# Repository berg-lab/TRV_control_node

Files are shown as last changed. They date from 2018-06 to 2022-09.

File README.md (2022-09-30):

# TRV_control_node
First generation radiator control based on Raspberry Pi Zero W

Refer to Paper: [Development and evaluation of an automatic steam radiator control system for retrofitting legacy heating systems in existing buildings](https://www.sciencedirect.com/science/article/abs/pii/S0378778821006289)

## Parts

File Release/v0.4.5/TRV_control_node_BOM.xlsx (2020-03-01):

Qty | Parts | Value | MPN | Device | Package | Description | PRICE
2 | RX, TX | LED | LG R971-KN-1 | LEDCHIPLED_0805 | CHIPLED_0805 | LED
1 | U4 | PCA9685 | PCA9685BS,118 | PCA9685HVQFN28 | HVQFN28_SOT788-1 | 16-channel 12-bit PWM
6 | C5, C6, C7, C11, C12, C15 | 0.1uF | GRM155R71C104KA88J | MICROBUILDER_CAP_CERAMIC_0402MP | MICROBUILDER__0402MP | Ceramic Capacitors
1 | C3 | 100uF | 12106D107MAT2A | C-USC1210 | C1210 | CAPACITOR, American symbol
4 | R6, R7, R8, R10 | 10K | RC0402JR-071KL | MICROBUILDER_RESISTOR_0402MP | MICROBUILDER__0402MP | Resistors
2 | R5, R9 | 10K | RC0402JR-0710KL | MICROBUILDER_RESISTOR_0402MP | MICROBUILDER__0402MP | Resistors
1 | R23 | 10K 0.1% | RNCF0402BTE10K0 | MICROBUILDER_RESISTOR_0402MP | MICROBUILDER__0402MP | Resistors
2 | C1, C8 | 10uF | GRJ155R60J106ME11D | MICROBUILDER_CAP_CERAMIC_0402MP | MICROBUILDER__0402MP | Ceramic Capacitors
1 | X1 | 16 MHz | CSTCE16M0V53-R0 | RESONATORSMD | RESONATOR-SMD | Resonator
2 | R19, R20 | 1K | RC0402JR-071KL | MICROBUILDER_RESISTOR_0402MP | MICROBUILDER__0402MP | Resistors
1 | R3 | 1K | RC0402JR-071KL | MICROBUILDER_RESISTOR_0402MP | MICROBUILDER__0402MP | Resistors
1 | C10 | 1uF | C0402C105K9PACTU | MICROBUILDER_CAP_CERAMIC_0402MP | MICROBUILDER__0402MP | Ceramic Capacitors
1 | R12 | 200K | RC0402FR-07200KL | MICROBUILDER_RESISTOR_0402MP | MICROBUILDER__0402MP | Resistors
1 | R1 | 220 | CRGCQ0402F220R | MICROBUILDER_RESISTOR_0402MP | MICROBUILDER__0402MP | Resistors
2 | R11, R15 | 27 | RC0402JR-0727RL | MICROBUILDER_RESISTOR_0402MP | MICROBUILDER__0402MP | Resistors
1 | J4 | 455-1750-1-ND | OSTVN03A150 | CONN_03 | 1X03 | Multi connection point. Often used as Generic Header-pin footprint for 0.1 inch spaced/style header connections
2 | R17, R18 | 470 | RC0402JR-07470RL | MICROBUILDER_RESISTOR_0402MP | MICROBUILDER__0402MP | Resistors
1 | U11 | 915MHz | RFM69HCW | RFM69HCW-915 | RFM69HCW-XXXS2 | Hope RF RFM69H ISM Transceiver Module
2 | J3, J6 | AMP FCI 10103594-0001LF | 10103594-0001LF | USB_MICRO-B_HALF_PTH | USB-MICROB-PTH | USB Type Micro-B Connector
1 | U5 | ATMEGA328P-MU | ATMEGA328P-MU | ATMEGA328P-MU | QFN50P500X500X100-33N | ATmega Series 20 MHz 32 KB Flash 2 KB SRAM 8-Bit Microcontroller - QFN-32 | 2.55 USD
1 | STAT | BLUE | LG R971-KN-1 | LED0805_NOOUTLINE | CHIPLED_0805_NOOUTLINE | LED
2 | SW1, SW2 | EVQQ | EVQ-Q2B03W | SWITCH_TACT_SMT_EVQQ2_SMALL | EVQ-Q2_SMALLER | SMT Tact Switches
1 | U2 | FT231XQ-R | FT231XQ-R | FT231XQ-R | FTDI_FT231XQ-R_PACKAGE | This is the 20-LD QFN package of the FTDI FT231XQ-R chip.
1 | U8 | MCP1703/3.3V | MCP1703T-3302E/CB | MCP1703CB | SOT23 | 250 mA, 16V, Low Quiescent Current LDO Regulator
1 | U$1 | OLED_091_SSD1306 | OLED_091_SSD1306 | OLED_091_SSD1306 | OLED_128X32_0.91
1 | U1 | PCA9306 | PCA9306DC,125 | PCA9306 | PSOP-8 | Bidirectional I2C level shifter
1 | RPI1 | RASPBERRYPI_BPLUS_BONNET_THMSMT | PPTC202LFBN-RC | RASPBERRYPI_BPLUS_BONNET_THMSMT | PI_BONNET_THMSMT
1 | D2 | STPS140Z | STPS140Z | MICROBUILDER_DIODE-SCHOTTKYSOD-123 | MICROBUILDER_SOD-123

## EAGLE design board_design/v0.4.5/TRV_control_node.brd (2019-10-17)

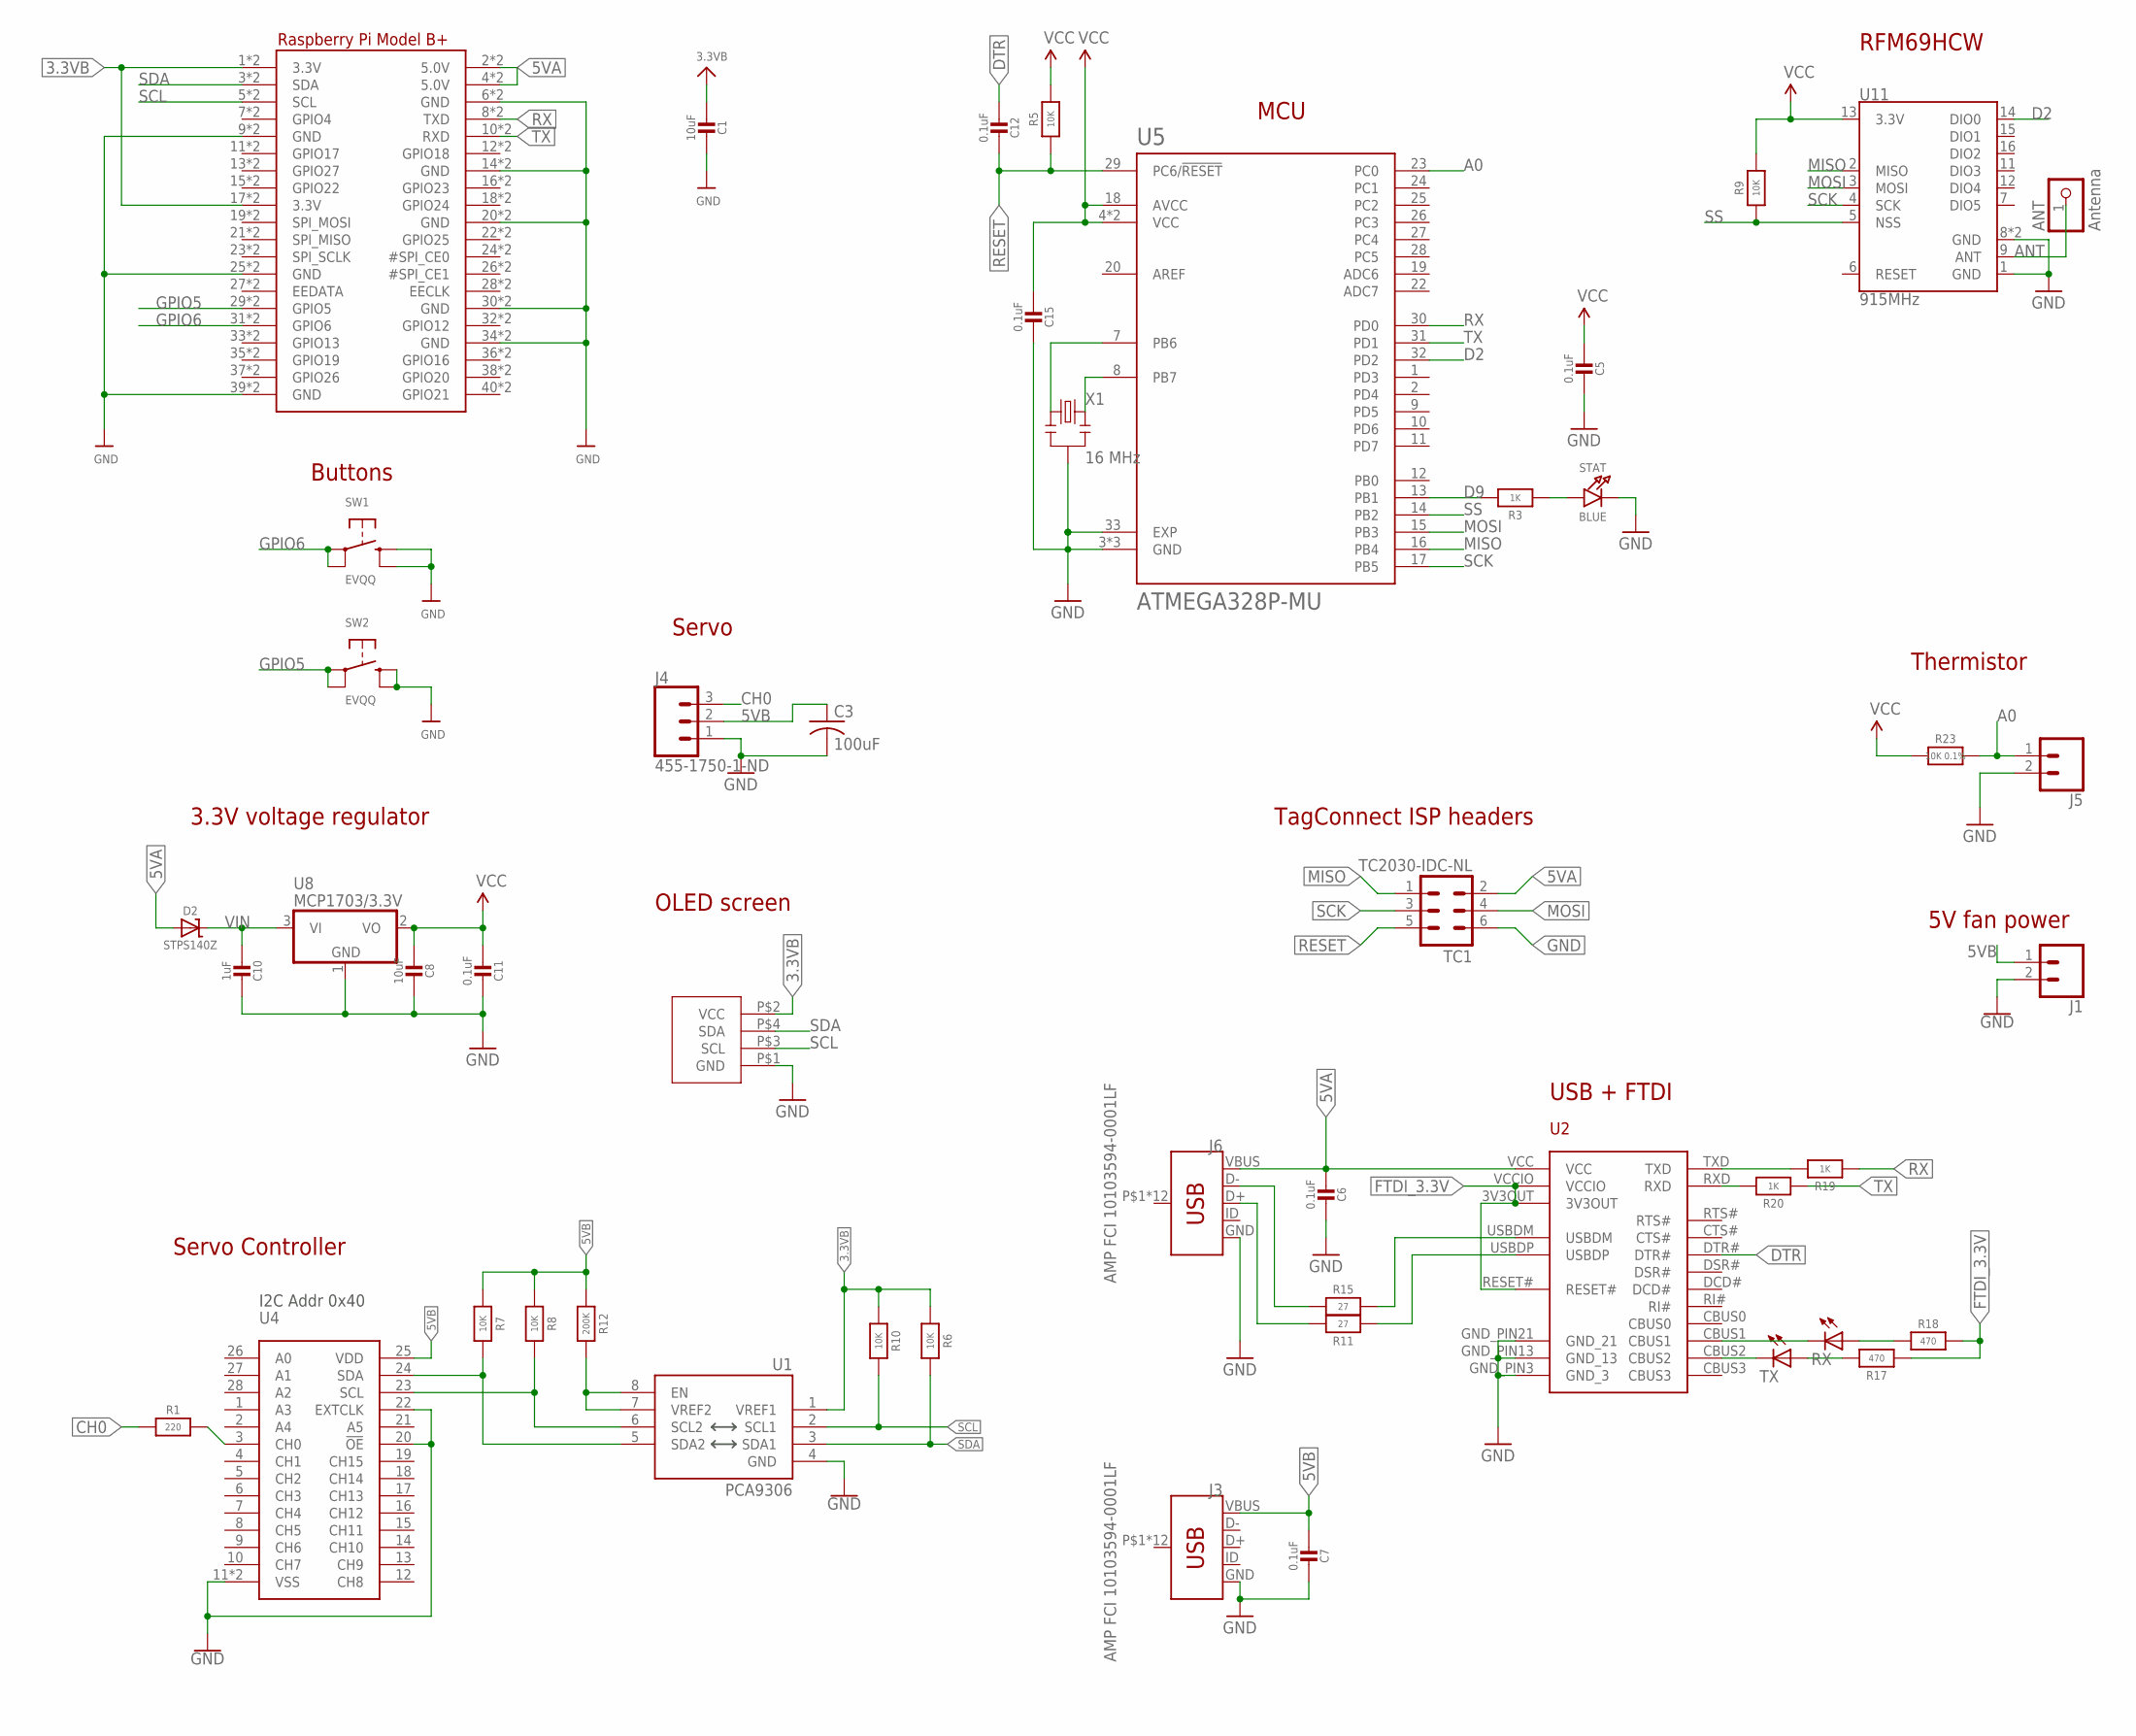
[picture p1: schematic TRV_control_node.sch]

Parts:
ANT: Antenna; 1X01-CLEANBIG; MPN Helical antenna
C1, C8: 10uF; MICROBUILDER__0402MP; MPN GRM155R71C104KA88J
C3: 100uF; C1210
C5, C6, C7, C11, C12, C15: 0.1uF; MICROBUILDER__0402MP; MPN GRM155R71C104KA88J
C10: 1uF; MICROBUILDER__0402MP; MPN GRM155R71C104KA88J
D2: STPS140Z; MICROBUILDER_SOD-123; MPN SD103AW-13-F
J1, J5: CONN_02; 1X02
J3, J6: AMP FCI 10103594-0001LF; USB-MICROB-PTH
J4: 455-1750-1-ND; 1X03
R1: 220; MICROBUILDER__0402MP; MPN RC0402JR-071KL
R3: 1K; MICROBUILDER__0402MP; MPN RC0402JR-0710KL
R5, R9: 10K; MICROBUILDER__0402MP; MPN RC0402JR-0710KL
R6, R7, R8, R10: 10K; MICROBUILDER__0402MP; MPN RC0402JR-071KL
R11, R15: 27; MICROBUILDER__0402MP; MPN RC0402JR-0727RL
R12: 200K; MICROBUILDER__0402MP; MPN RC0402JR-071KL
R17, R18: 470; MICROBUILDER__0402MP; MPN RC0402JR-07470RL
R19, R20: 1K; MICROBUILDER__0402MP; MPN RC0402JR-071KL
R23: 10K 0.1%; MICROBUILDER__0402MP; MPN RC0402JR-0727RL
RPI1: RASPBERRYPI_BPLUS_BONNET_THMSMT; PI_BONNET_THMSMT
RX: LEDCHIPLED_0805; CHIPLED_0805; MPN LG R971-KN-1
STAT: BLUE; CHIPLED_0805_NOOUTLINE
SW1, SW2: EVQQ; EVQ-Q2_SMALLER
TC1: TC2030-IDC-NL
TX: LEDCHIPLED_0805; CHIPLED_0805; MPN LG R971-KN-1
U1: PCA9306; PSOP-8
U2: FT231XQ-R; FTDI_FT231XQ-R_PACKAGE; MPN FT231XQ-R
U4: PCA9685HVQFN28; HVQFN28_SOT788-1
U5: ATMEGA328P-MU; QFN50P500X500X100-33N; MPN ATMEGA328P-MU
U8: MCP1703/3.3V; SOT23; MPN MCP1703T-3302E/CB
U11: 915MHz; RFM69HCW-XXXS2; MPN RFM69HCW
U$1: OLED_091_SSD1306; OLED_128X32_0.91
X1: 16 MHz; RESONATOR-SMD; MPN CSTCE16M0V53-R0

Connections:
3.3VB: C1.2, R6.1, R10.1, RPI1.1 (3.3V), RPI1.17 (3.3V), RPI1.S1 (3.3V), RPI1.S17 (3.3V), U1.1 (VREF1), U$1.P$2 (VCC)
5VA: C6.2, D2.A, J6.VBUS, RPI1.2 (5.0V), RPI1.4 (5.0V), RPI1.S2 (5.0V), RPI1.S4 (5.0V), TC1.2, U2.VCC
5VB: C3.1, C7.2, J1.1, J3.VBUS, J4.2, R7.1, R8.1, R12.1, U4.25 (VDD)
A0: J5.1, R23.2, U5.23 (PC0)
ANT: ANT.1, U11.9 (ANT)
CH0: J4.3, R1.1
D2: U5.32 (PD2), U11.14 (DIO0)
D9: R3.2, U5.13 (PB1)
DTR: C12.2, U2.DTR#
FTDI_3.3V: R17.1, R18.2, U2.3V3OUT, U2.RESET#, U2.VCCIO
GND: C1.1, C3.2, C5.1, C6.1, C7.1, C8.1, C10.1, C11.1, C15.1, J1.2, J3.GND, J4.1, J5.2, J6.GND, RPI1.6 (GND), RPI1.9 (GND), RPI1.14 (GND), RPI1.20 (GND), RPI1.25 (GND), RPI1.30 (GND), RPI1.34 (GND), RPI1.39 (GND), RPI1.S6 (GND), RPI1.S9 (GND), RPI1.S14 (GND), RPI1.S20 (GND), RPI1.S25 (GND), RPI1.S30 (GND), RPI1.S34 (GND), RPI1.S39 (GND), STAT.C, SW1.B (S), SW1.B' (S1), SW2.B (S), SW2.B' (S1), TC1.6, U1.4 (GND), U2.GND_PIN3 (GND_3), U2.GND_PIN13 (GND_13), U2.GND_PIN21 (GND_21), U4.11 (VSS), U4.20 (!OE), U4.22 (EXTCLK), U4.TH (VSS), U5.3 (GND), U5.5 (GND), U5.21 (GND), U5.33 (EXP), U8.1 (GND), U11.1 (GND), U11.8 (GND), U11.10 (GND), U$1.P$1 (GND), X1.2
GPIO5: RPI1.29 (GPIO5), RPI1.S29 (GPIO5), SW2.A, SW2.A' (P1)
GPIO6: RPI1.31 (GPIO6), RPI1.S31 (GPIO6), SW1.A, SW1.A' (P1)
MISO: TC1.1, U5.16 (PB4), U11.2 (MISO)
MOSI: TC1.4, U5.15 (PB3), U11.3 (MOSI)
unnamed: R12.2, U1.7 (VREF2), U1.8 (EN)
unnamed: R20.2, U2.RXD
unnamed: R19.2, U2.TXD
unnamed: U5.8 (PB7), X1.3
unnamed: U5.7 (PB6), X1.1
unnamed: R8.2, U1.6 (SCL2), U4.23 (SCL)
unnamed: R7.2, U1.5 (SDA2), U4.24 (SDA)
unnamed: R3.1, STAT.A
unnamed: R1.2, U4.3 (CH0)
unnamed: RX.C, U2.CBUS1
unnamed: TX.C, U2.CBUS2
unnamed: R15.2, U2.USBDM
unnamed: R11.1, U2.USBDP
unnamed: R18.1, RX.A
unnamed: R17.2, TX.A
unnamed: J6.D-, R15.1
unnamed: J6.D+, R11.2
RESET: C12.1, R5.1, TC1.5, U5.29 (PC6/!RESET)
RX: R19.1, RPI1.8 (TXD), RPI1.S8 (TXD), U5.30 (PD0)
SCK: TC1.3, U5.17 (PB5), U11.4 (SCK)
SCL: R10.2, RPI1.5 (SCL), RPI1.S5 (SCL), U1.2 (SCL1), U$1.P$3 (SCL)
SDA: R6.2, RPI1.3 (SDA), RPI1.S3 (SDA), U1.3 (SDA1), U$1.P$4 (SDA)
SS: R9.1, U5.14 (PB2), U11.5 (NSS)
TX: R20.1, RPI1.10 (RXD), RPI1.S10 (RXD), U5.31 (PD1)
VCC: C5.2, C8.2, C11.2, C15.2, R5.2, R9.2, R23.1, U5.4 (VCC), U5.6 (VCC), U5.18 (AVCC), U8.2 (VO), U11.13 (3.3V)
VIN: C10.2, D2.C, U8.3 (VI)

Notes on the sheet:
MCU
USB + FTDI
RFM69HCW
TagConnect ISP headers
3.3V voltage regulator
I2C Addr 0x40
Servo
Servo Controller
OLED screen
Buttons
Thermistor
5V fan power

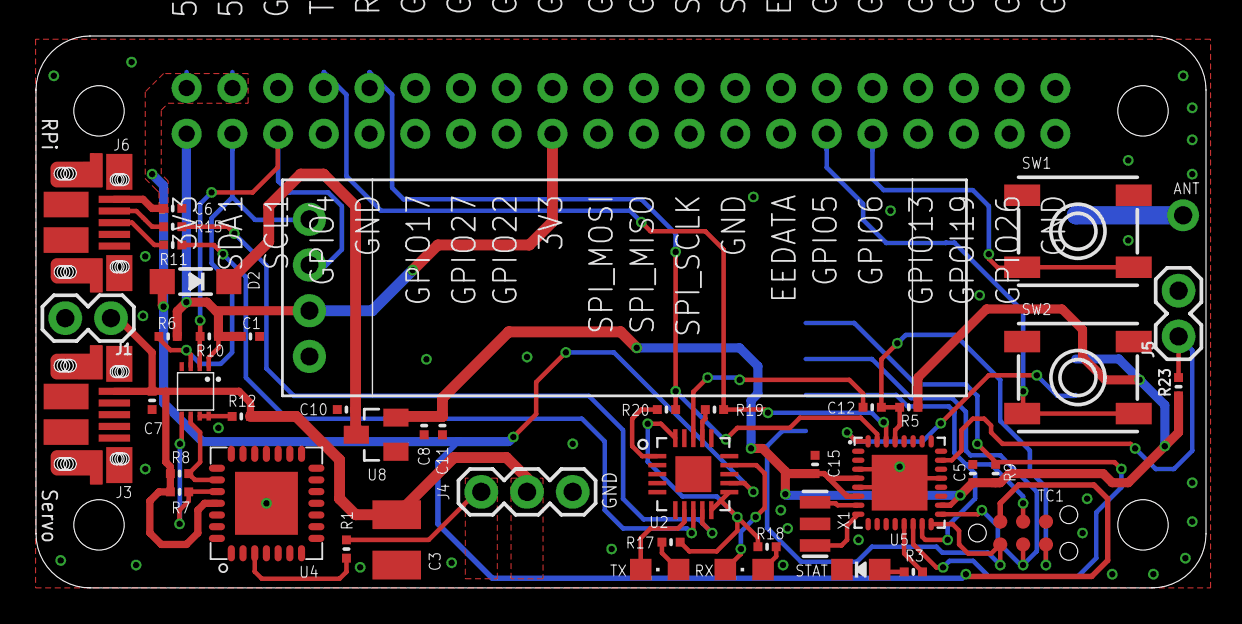
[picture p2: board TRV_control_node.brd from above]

Board: 2 copper layers, 65.0 x 30.7 mm, 48 parts (1 on the bottom side), 41 nets.

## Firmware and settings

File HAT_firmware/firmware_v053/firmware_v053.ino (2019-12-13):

// Control node wireless data processor v0.5.3

// Updated on 12/13/2019
// Developed by Akram Ali

#include <RFM69.h>  //  https://github.com/LowPowerLab/RFM69
#include <SPI.h>

// define node parameters
//#define NODEID              120 // must be unique for each node on same network (range up to 254, 0 is broadcast)
uint16_t NODEID =             120; // same as above, but supports 10bit addresses (up to 1023 node IDs)
#define NETWORKID             120
#define GATEWAYID             1
#define GATEWAY_NETWORKID     1
#define ENCRYPTKEY            "Tt-Mh=SQ#dn#JY3_"
#define FREQUENCY             RF69_915MHZ //Match this with the version of your Moteino! (others: RF69_433MHZ, RF69_868MHZ)
#define IS_RFM69HW            //uncomment only for RFM69HW! Leave out if you have RFM69W!
#define LED                   9 // led pin

// define objects
RFM69 radio;

// define other global variables
int setpoint, manual_override, pwm = 0;
char dataPacket[150];
char dataPacket2[60];
char data[100];
char _rssi[5];
unsigned long t;

// global variables for parsing serial data
const byte numChars = 32;
char receivedChars[numChars];
char tempChars[numChars];        // temporary array for use when parsing
char messageFromPC[numChars] = {0};
boolean newData = false;

void setup()
{
  pinMode(10, OUTPUT); // Radio SS pin set as output
  Serial.begin(115200);
  fadeLED();
  
  radio.initialize(FREQUENCY,NODEID,NETWORKID);
#ifdef IS_RFM69HW
  radio.setHighPower(); //uncomment only for RFM69HW!
#endif
  radio.encrypt(ENCRYPTKEY);

  t = millis();
}

void loop()
{
    recvWithStartEndMarkers();
    if (newData == true)
    {
      strcpy(tempChars, receivedChars);
          // this temporary copy is necessary to protect the original data
          //   because strtok() used in parseData() replaces the commas with \0
      parseData();
      newData = false;
      
      readSensors();
      // send datapacket to gateway
      radio.setNetwork(GATEWAY_NETWORKID);
      radio.sendWithRetry(GATEWAYID, dataPacket, strlen(dataPacket));  // send data
      radio.setNetwork(NETWORKID);
      Serial.println(dataPacket);
      memset(dataPacket, 0, sizeof dataPacket);   // clear array
      Blink(LED,5);
    }
    
//  while(Serial.available() > 0)    // check if there is serial data
//  {
//    char a[2];
//    if(Serial.find("SET"))   // find setpoint
//    {
//      Serial.readBytes(a, 2);   // expecting two bytes after "SET"
//
//      setpoint = a[0] - 48;   // convert ASCII char value to number value ('0' in ASCII is 48)
//      manual_override = a[1] - 48;
//      readSensors();
//
//      delay(5);
//      
//      // send datapacket to gateway
//      radio.setNetwork(GATEWAY_NETWORKID);
//      radio.sendWithRetry(GATEWAYID, dataPacket, strlen(dataPacket));  // send data
//      radio.setNetwork(NETWORKID);
//      
//      memset(dataPacket, 0, sizeof dataPacket);   // clear array
//    
//      Blink(LED,5);
//    }
//    else
//      break;
//  }

  if (radio.receiveDone())
  {
    int rssi = radio.RSSI;

    if (radio.DATALEN > 0)
    {
      for (byte i = 0; i < radio.DATALEN; i++)
        data[i] = (char)radio.DATA[i];
    }

    if (radio.ACKRequested())
    {
      //byte theNodeID = radio.SENDERID;
      radio.sendACK();
      
      dtostrf(rssi, 3, 0, _rssi);
      strcat(data, ",r:");
      strcat(data, _rssi);

      Serial.println(data);
      delay(1);

      memset(data, 0, sizeof data);
      memset(_rssi, 0, sizeof _rssi);

      Blink(LED,5);
    }
  }

  if((unsigned long)(millis()-t) >= 30000)    // send temp data approximately every 30 secs
  {
    getTemperature();

    // send datapacket to gateway
    radio.setNetwork(GATEWAY_NETWORKID);
    radio.sendWithRetry(GATEWAYID, dataPacket2, strlen(dataPacket2));  // send data
    radio.setNetwork(NETWORKID);

    Serial.println(dataPacket2);
    delay(1);
    
    memset(dataPacket2, 0, sizeof dataPacket2);   // clear array
  
    Blink(LED,5);
    t = millis();
  }

  
}


void getTemperature()
{
  // external temp reading
  float adc = averageADC(A0);
  float R = resistance(adc, 10000); // Replace 10,000 ohm with the actual resistance of the resistor measured using a multimeter (e.g. 9880 ohm)
  float a = steinhart_2(R);  // get temperature from thermistor using the custom Steinhart-hart equation

  // define character arrays for all variables
  char _i[3]="";
  char _a[7]="";

  // convert all flaoting point and integer variables into character arrays
  int _nodeID = (int)NODEID + 4;    // node ID of radiator surface temp
  dtostrf(_nodeID, 1, 0, _i);
  dtostrf(a, 3, 2, _a);   // this function converts float into char array. 3 is minimum width, 2 is decimal precision
  delay(1);

  memset(dataPacket2, 0, sizeof dataPacket2);   // clear array

  // create datapacket by combining all character arrays into a large character array
  strcat(dataPacket2, "i:");
  strcat(dataPacket2, _i);
  strcat(dataPacket2, ",a:");
  strcat(dataPacket2, _a);
  delay(5);
}



void readSensors()
{
  //setpoint = 0;
  
  // define character arrays for all variables
  char _i[4];
  char _y[2];
  char _u[2];
  char _w[4];

  // convert all flaoting point and integer variables into character arrays
  dtostrf(NODEID, 1, 0, _i);
  dtostrf(setpoint, 1, 0, _y);
  dtostrf(manual_override, 1, 0, _u);
  dtostrf(pwm, 1, 0, _w);
  delay(5);

  dataPacket[0] = 0;  // first value of dataPacket should be a 0

  // create datapacket by combining all character arrays into a large character array
  strcat(dataPacket, "i:");
  strcat(dataPacket, _i);
  strcat(dataPacket, ",y:");
  strcat(dataPacket, _y);
  strcat(dataPacket, ",u:");
  strcat(dataPacket, _u);
  strcat(dataPacket, ",w:");
  strcat(dataPacket, _w);
  delay(5);
}


// Averaging ADC values to counter noise in readings  *********************************************
float averageADC(int pin)
{
  float sum=0.0;
  for(int i=0;i<5;i++)
  {
     sum = sum + analogRead(pin);
  }
  float average = sum/5.0;
  return average;
}

// Get resistance ****************************************************************
float resistance(float adc, int true_R)
{
  float R = true_R/(1023.0/adc-1.0);   // convert 10-bit reading into resistance
//  float ADCvalue = adc*(8.192/3.3);  // Vcc = 8.192 on GAIN_ONE setting, Arduino Vcc = 3.3V in this case
//  float R = 10000/(65535/ADCvalue-1);  // 65535 refers to 16-bit number
  return R;
}


// Get temperature from Steinhart equation (10K Precision Epoxy Thermistor - 3950 NTC) *****************
float steinhart_2(float R)
{
  float steinhart;
  steinhart = R / 10000;     // (R/Ro)
  steinhart = log(steinhart);                  // ln(R/Ro)
  steinhart /= 3950.0;                   // 1/B * ln(R/Ro)
  steinhart += 1.0 / (25.0 + 273.15); // + (1/To)
  steinhart = 1.0 / steinhart;                 // Invert
  steinhart -= 273.15;                         // convert to C

  return steinhart;
}


void Blink(byte PIN, int DELAY_MS)
{
  pinMode(PIN, OUTPUT);
  digitalWrite(PIN,HIGH);
  delay(DELAY_MS);
  digitalWrite(PIN,LOW);
}

// Fade LED *****************************************
void fadeLED()
{
  int brightness = 0;
  int fadeAmount = 5;
  for(int i=0; i<510; i=i+5)  // 255 is max analog value, 255 * 2 = 510
  {
    analogWrite(LED, brightness);  // pin 9 is LED
  
    // change the brightness for next time through the loop:
    brightness = brightness + fadeAmount;  // increment brightness level by 5 each time (0 is lowest, 255 is highest)
  
    // reverse the direction of the fading at the ends of the fade:
    if (brightness <= 0 || brightness >= 255)
    {
      fadeAmount = -fadeAmount;
    }
    // wait for 20-30 milliseconds to see the dimming effect
    delay(10);
  }
  digitalWrite(LED, LOW); // switch LED off at the end of fade
}


// Parse Data *****************************************
void parseData() {      // split the data into its parts

    char * strtokIndx; // this is used by strtok() as an index

    strtokIndx = strtok(tempChars,",");      // get the first part - the string
    setpoint = atoi(strtokIndx);     // convert this part to an integer
 
    strtokIndx = strtok(NULL, ","); // this continues where the previous call left off
    manual_override = atoi(strtokIndx);     // convert this part to an integer

    strtokIndx = strtok(NULL, ","); // this continues where the previous call left off
    pwm = atoi(strtokIndx);     // convert this part to an integer
}

// Receive serial data *****************************************
void recvWithStartEndMarkers() {
    static boolean recvInProgress = false;
    static byte ndx = 0;
    char startMarker = '<';
    char endMarker = '>';
    char rc;

    while (Serial.available() > 0 && newData == false) {
        rc = Serial.read();

        if (recvInProgress == true) {
            if (rc != endMarker) {
                receivedChars[ndx] = rc;
                ndx++;
                if (ndx >= numChars) {
                    ndx = numChars - 1;
                }
            }
            else {
                receivedChars[ndx] = '\0'; // terminate the string
                recvInProgress = false;
                ndx = 0;
                newData = true;
            }
        }

        else if (rc == startMarker) {
            recvInProgress = true;
        }
    }
}

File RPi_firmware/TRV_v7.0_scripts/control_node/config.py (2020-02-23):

# -*- coding: utf-8 -*-

# This script gets configuration settings for the node from the server
# and saves it to local JSON file. It also sends back MAC and IP addresses,
# along with current date time and running scripts back to the server,
# and sets automation scripts on the node.

# Developed by Akram Ali
# Last updated on: 02/23/2020

import os
import requests
import json
import time
import socket
import shlex
import subprocess
from pathlib import Path
from datetime import datetime

url = 'config.elemental-platform.com'
get_url = 'http://config.elemental-platform.com/wp-json/acf/v3/nodes?slug[]='
put_url = 'http://config.elemental-platform.com/wp-json/acf/v3/nodes/'
auth = ('node', 'vvET(G6^kmkhx)l!!Zqnd@)^')

control_strategies = ['manual', 'enforced_schedule', 'check_motion', 'pid_temp', 'pid_temp_motion']
scripts = ['config','read_GPIO', 'read_serial', 'write_serial','set_PWM','operative_temp','datalogger',
'monitor_core_temp','preheat','enforce_schedule','check_motion','pid_temp'] # set all scripts to check if they're running
reboot_flag = False
put_config_flag = False

control_node_id_dir = '/home/pi/control_node'
json_dir = '/home/pi/control_node/'
temp_data_dir = '/home/pi/datalogger/temp_data'

node_id = [".".join(f.split(".")[:-1]) for f in os.listdir(control_node_id_dir) if f.endswith(".node")]    # get node ID
wp_id = 0

mac = subprocess.check_output('cat /sys/class/net/wlan0/address', shell=True).strip()

time.sleep(0.1)	# give some time for wifi to connect and everything to load and settle down

# get IP address
def get_ip_address():
	try:
		ip = subprocess.check_output("hostname -I | cut -d' ' -f1", shell=True).strip()
		if ':' not in ip: # check if it's IPv4 and not local IPv6
			return ip
		else:
			return ''
	except:
		pass
		return ''
	

# check internet connection
def internet_connection():
	try:
		host = socket.gethostbyname(url)
		s = socket.create_connection((host, 80), 2)
		s.close()
		return True
	except:
		pass
	return False

# get current running scripts
def get_running_scripts():
	PIDs=[]
	script_status=[]
	ss = ''
	for s in scripts:
		cmd = "pgrep -f 'python %s.py'" % s
		try:
			output = subprocess.check_output(shlex.split(cmd), shell=False).decode("utf-8")
		except subprocess.CalledProcessError:
			output = ''
		PIDs.append(output)
		time.sleep(0.01)
	n=0

	for p in PIDs:
		n+=1
		if n == 7 or n == 9:
			script_status.append(' ')
		if p == '':
			script_status.append('0')
		else:
			script_status.append('1')
	ss = ''.join(script_status)
	return ss

# get node configuration from server
def get_config():
	global wp_id

	attempts = 0
	while attempts < 3:
		try:
			_response = requests.get(get_url+str(node_id), auth=auth)
			wp_id = _response.json()[0]['id']
			break
		except:
			attempts += 1
			time.sleep(1)
			_response = {}	# return empty json file
	return _response

# send back mac and ip address to server
def put_config(put_type):
	global wp_id
	global mac
	global ip

	# get node statuses
	running_scripts = get_running_scripts()
	last_updated = str(datetime.now().strftime('%Y/%m/%d %H:%M:%S'))
	ct = os.popen("vcgencmd measure_temp").read()
	ct2 = ct.replace("temp=","")
	ct3 = ct2.replace("'C","")
	core_temp = ct3.replace("\n","")
	pwm = get_PWM()
	if config[0]['acf']['servo_type'] == 'normal':
		s_start = 635
		s_end = 150
	elif config[0]['acf']['servo_type'] == 'special_servo':
		s_start = 600
		s_end = 130
	pwm_percent = round((1 - ((float(pwm) - s_end)/(s_start - s_end))) * 100)
	current_valve_position = "%s%% (%s)" % (str(int(pwm_percent)), pwm)

	network_info = {
		"fields": {
			"mac_address": mac,
			"ip_address": ip
		}
	}

	status = {
		"fields": {
			"last_updated": last_updated,
			"running_scripts": running_scripts,
			"core_temp": str(core_temp),
			"current_valve_position": current_valve_position
		}
	}

	reboot = {
		"fields": {
			"reboot": False
		}
	}

	setpoint = {
		"fields": {
			"override_setpoint": False
		}
	}

	if put_type == 'network':
		json_body = network_info
	elif put_type == 'status':
		json_body = status
	elif put_type == 'reboot':
		json_body = reboot
	elif put_type == 'override_setpoint':
		json_body = setpoint

	attempts = 0
	while attempts < 3:
		try:
			_response = requests.put(put_url+str(wp_id), json=json_body, auth=auth)
			time.sleep(1)
			if _response:
				return True
			else:
				return False
			break
		except:
			attempts += 1
			time.sleep(1)
			_response = {}
	return False
	

# save config json file
def save_config(response_json):
	attempts = 0
	while attempts < 3:
		try:
			with open(json_dir + 'config.json', 'w') as f:
				json.dump(response_json, f, ensure_ascii=False, indent=4)
			break
		except:
			attempts += 1
			time.sleep(0.1)

# rewrite old config json file
def save_old_config(response_json):
	attempts = 0
	while attempts < 3:
		try:
			with open(json_dir + '_config.json', 'w') as f:
				json.dump(response_json, f, ensure_ascii=False, indent=4)
			break
		except:
			attempts += 1
			time.sleep(0.1)

# read config json file
def load_config():
	attempts = 0
	while attempts < 3:
		try:
			with open(json_dir + 'config.json', 'r') as f:
				data = json.load(f)
			break
		except:
			attempts += 1
			time.sleep(0.1)
	return data

# read old config json file
def load_old_config():
	attempts = 0
	while attempts < 3:
		try:
			with open(json_dir + '_config.json', 'r') as f:
				data = json.load(f)
			break
		except:
			attempts += 1
			time.sleep(0.1)
	return data


# dump config json file
def dump_config(config, key, value):
	config[0]['acf'][key] = value

	attempts = 0
	while attempts < 3:
		try:
			with open(json_dir + 'config.json', 'w') as f:
				json.dump(config, f, indent=4)
			break
		except:
			attempts += 1
			time.sleep(0.1)

# get latest PWM value from file
def get_PWM():
	try:
		file = open('%s/%s.csv' % (temp_data_dir, node_id[0]),'r')
		data = file.readline()
		file.close()
	except:
		pass
	parsed_data = {}
	try:
		for p in data.strip().split(","): #strip() removes trailing \n
			k,v = p.split(":")
			parsed_data[k] = v if v else 0.00
		pwm = parsed_data.get('w')
		return pwm
	except:
		return 0

# delete old config files
def del_file(_file):
	fn = '%s/%s' % (control_node_id_dir, _file)
	my_file = Path(fn)
	if my_file.is_file():   # check if files exist
		os.remove(fn)   # delete file
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

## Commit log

2018-06-01 schematic changes
    [TRV_control_node.brd, TRV_control_node.sch]
2018-06-04 Arranged components on brd
    [TRV_control_node.brd, TRV_control_node.sch]
2018-06-05 Completed routing
    [TRV_control_node.brd, TRV_control_node.sch]
2018-06-05 Adjustments
    - Removed second OLED screen pins
    - Moved USB ports slightly away from each other
    - Silkscreen adjustments
    [TRV_control_node.brd, TRV_control_node.sch]
2018-06-06 USB ports adjustment
    - Moved USB ports a bit further away
    - Some trace adjustments
    - ERC and DRC
    - Some silkscreen adjustments
    [TRV_control_node.brd, TRV_control_node.sch]
2018-06-07 v0.4.1 - update
    - Changed TSSOP28 package for PCA9685 to HVQFN28
    - Moved 3.3V vreg from under the OLED to right below it
    - Trace adjustments
    - Exported gerbers for v0.4.0 and v0.4.1
    - ERC & DRC check
    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
    [TRV_control_node.brd, TRV_control_node.sch]
2018-06-07 vreg adjustment
    Moved the Vreg and its caps a bit away from the 3 pin servo header
    [TRV_control_node.brd]
2018-06-07 added updated gerbers
2018-07-18 v0.4.2 - bug fixes
    - Connected SDA and SCL for servo control (had incorrect net names in schematic)
    - Fixed servo header pins (sig and power were flipped)
    - Silkscreen adjustment
    - Maintained same tcream (components weren't moved) - can reuse stencil for v0.4.1
    - DRC
    [TRV_control_node.brd, TRV_control_node.sch]
2018-07-19 small update
    - Moved via a bit
    - Removed some wire stubs
    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
    [TRV_control_node.brd, TRV_control_node.sch]
2018-08-21 v0.4.3 - small update
    - Moved 3 pin servo header back to allow right-angled male pins or just wires to be directly soldered there
    - Moved ANT via to the corner of board
    - Moved buttons a bit lower
    - Added header for analog input (thermistor with 10K resistor pad)
    - Silkscreen and trace adjustments to accomodate design update
    - ERC/DRC
    [TRV_control_node.brd, TRV_control_node.sch]
2018-08-21 silkscreen update + added gerbers
    [TRV_control_node.brd]
2018-09-04 v0.4.2b & v0.4.3 - proper versioning & update
    - Renamed v0.4.3 to v0.4.2b -- this design is not used as some parts are physically "moved" on the board.
    - v0.4.3 - this design now incorporates the following:
    - thermistor header pins for extra temperature monitoring if needed
    - Relocation of antenna hole away from buttons
    - Added SMD pads for servo
    - silkscreen update
    [TRV_control_node.brd, TRV_control_node.sch]
2018-09-04 Updated gerber files
2018-09-06 Added gerbers for v0.4.3
2018-10-15 V0.4.4 - added fan power pins breakout
    - moved some traces
    - adjusted vias
    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
    [TRV_control_node.brd, TRV_control_node.sch]
2018-10-15 Added v0.4.4 gerbers
2018-10-15 updated antenna trace
    moved antenna pin header to the side to allow easy soldering
    [TRV_control_node.brd]
2018-10-30 ID, ATC, serial
    - Updated network and gateway IDs - now switches network ID on the fly
    - Default send with retry
    - Radio ATC
    - Now reads entire string instead of just one char - a bit slower but necessary for sending full packets to gateway
    - Removed RSSI from room node (gateway should append it either way)
2018-11-21 v0.5.1 firmware update
    - Added fadeLED to indicate boot/reset
    - Serial available now checks for "SET" to read setpoint and manual override
    - updated ACK for local nodes
    - added code to read thermistor every ~30 sec and send data
    - adjusted memset and other minor code fixes
    - added code for bare sender: only checks serial for "SET" and sends data
    [firmware_v051.ino.ino, firmware_v051_bare_sender.ino]
2019-05-02 Added RPi firmware
    also reorganized the directory structure
    [TRV_control_node.brd, TRV_control_node.sch, _s.csv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]
2019-05-02 moved board design files
    [TRV_control_node.brd, TRV_control_node.sch]
2019-10-17 v0.4.5
    - Added silkscreen at the back of the board for Node IDs
    - Changed soldermask limit to 14mil to cover vias for a cleaner look
    - functionally same board as v0.4.4 - no other trace or component changes
    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
    [TRV_control_node.brd, TRV_control_node.sch]
2019-10-17 Added gerbers for v0.4.5
2019-10-17 updated gerbers to exclude tNames layer
2019-10-30 v0.5.2 - RPi firmware
    - Added diagnostics in readGPIO firmware that checks and running scripts, displays IP address, disk space and current data time. Access diagnostic by pressing and holding both buttons for 3 seconds. 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
2019-12-13 updated HAT firmware - v0.53
    - fixed split of setpoint and manual override
    - also added PWM values to be sent
    Explanation of changes: now allows setpoint values larger than 1 digit and expects the format: "<71,1, 243>" where '<' and '>' are start and end markers and 71 is setpoint (could also be 5, for example), 1 is manual override, and 243 is PWM value.
    - PWM value takes the key 'w' in the dictionary
    [firmware_v053.ino]
2019-12-18 Added v5.3 scripts
    small change in firmware of Pi and HAT
    [_s.csv, auto.csv, m.csv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]
2019-12-18 v6.0 - major update
    - everything now comes from a config file from server.
    - all scripts updated to check config file and respond in real time
    - added new control strategy - pid control for temp and pid control with motion detection
    - many many minor bug fixes and exception handling
    - screen rotation on the fly
    - everything controlled by GUI - can even set servo type and control strategy as needed
    - many other changes not listed in changelog
    not working yet - PWM values still not being saved in temp file
    [_s.csv, auto.csv, m.csv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]
2019-12-18 v6.1 - update
    - now logging PID values as well
    - other minor bug fixes
    - forgot to mention in previous update - version number now changed to v6.1 instead of v0.6.1. Ready for prime time!
    [_s.csv, auto.csv, m.csv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]
2019-12-18 Update read_GPIO.py
    - minor bug fix to account for different control strategies
    [read_GPIO.py]
2019-12-18 Update read_GPIO.py
    - bug fix: save proper setpoint at boot so the temp setpoint in file matches the control strategy selected
    [read_GPIO.py]
2019-12-18 Update read_GPIO.py
    - fixed screen rotation and screen not loading up on boot
    [read_GPIO.py]
2019-12-20 v6.0 HAT firmware
    - same as v053, except serial print for node ID is now removed
2019-12-22 updated config.py
    - fixed getting node info from slug via acf
    - delete config file on boot and create new file
    [temp_setpoint.csv]
2019-12-23 Update firmware_v6.0.ino
    - fixed node id
    - added handling of node id by radio packet and appending it (from sensor data)
    - fixed handling of radiator surface temperature datapacket
    - automatic changing of node ID in the RFM69 library to assign different node ID for surface temp node
    - removed old code for setpoint id
    [firmware_v6.0.ino]
2019-12-25 minor updates
    - fixed some time delays and some handling of things in various scripts
    [config.py, read_serial.py]
2019-12-28 Update read_GPIO.py
    updatedsave setpoint command - now there is a separate save for start (where manual override is initially 0), and save is removed every 30 seconds. Setpoint is now only updated when button is pressed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
2020-02-11 v6.2 update
    - datalogger function updated to initialize temp motion data file with no motion. This helps the checkmotion script to run on boot
    - config file updated to push proper IPv4 address and retry when no address available
    - config file also handles empty JSON response better so it doesn't crash the script entirely
    - added proper reboot flag to config file so node can be rebooted from server when needed
    - IP address and status now updated every hour
    - read GPIO function updated to display proper IPv4 address only (also version update on screen)
    - added PEAP settings for wpa_supplicant file
    - PID function now updated to tune the current temp reading. This can be done by an "offset" (set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
    [_s.csv, auto.csv, m.csv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]
2020-02-13 fixed variable class bug
    - made pid temp offest a global variable, so it actually takes the values from server
2020-02-13 feature update - dynamic setpoints + PID
    - fixed PID tunings
    - read_GPIO now gets the upper and lower setpoint limits from server
    - same with temp setpoints
    - set_PWM now gets step size from server - can be dynamically adjusted
    [read_GPIO.py, set_PWM.py]
2020-02-13 bug fixes
    - temp offset is now float
    - moved temp upper and lower limits into if else blocks
    [read_GPIO.py]
2020-02-14 bug fix
    - type cast to int
    [read_GPIO.py]
2020-02-14 bug fix 2
    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
    [set_PWM.py]
2020-02-17 v7.0 - major update
    - This update changes a lot of the functionality of the nodes - incompatible with previous versions
    - Reboot and override flag iare now locally set in file as well as pushed to server to prevent bootloop and override loop
    - Added check motion "value", which allows either a custom setpoint value to be set after motion is detected, or the previously set value. Value retrived from server
    - CPU core temp is now sent to server
    - PWM value is now sent to server in raw as well as percentage of valve closed
    - dictionary updated to add new PID components as well as changed w to PWM, and x to PID output
    - _s.csv file is now moved to temp_data dir and renamed to nodeID_old
    - read GP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
    [preheat.csv]
2020-02-17 bug fix with type casting PWM percentage
    also added missing temp_data_dir
    [config.py]
2020-02-17 bug fixes
    - send status every 10 mins, send network every hour
    - save setpoint bug fix - based on control strategy
    [config.py, read_GPIO.py, set_PWM.py]
2020-02-17 datalogger script fix
    - added PID components to sensorTypes
    - commented out initial control node temp file - just need to wait for new data to come through instead
2020-02-18 manual override discrepancy fix
    - added proper reading of manual override in all scripts
    - should fix bug with random failed setpoint writes to file
    [read_GPIO.py, set_PWM.py]
2020-02-18 added temp files
    [200.csv]
2020-02-23 added operative temp
    - new script that calculates operative temp based on globe temp and air temp and saves to file
    - all necessary scripts upgraded to switch between operantive and air temp
    - rc.local also updated to start operative temp script
    - new entry in dictionary
    - readgpio running scripts now have operative temp as extra script
2020-02-23 setpoint step size bug fix
    default values assigned; script checks if config file contains step size and won't crash even if it doesn't
    [read_GPIO.py, set_PWM.py]
2020-02-23 Update read_GPIO.py
    adding try except so script doesn't fail
    [read_GPIO.py]
2020-02-24 dangerous bug fix
    BUILDING BURNING BECAUSE PID KEPT ALL VALVES OPEN!
    - bug was filename took 2 arguments in string format, but 3 provided. Fixed scripts now
2020-02-27 Update pid_temp.py
    - only change pwm value if it's significantly different from previous value. If they're same, don't apply. Hopefully this removes stress from servo and prevents it from constantly going to a position it's already at.
2020-03-01 added BOM
    [TRV_control_node_BOM.xlsx]

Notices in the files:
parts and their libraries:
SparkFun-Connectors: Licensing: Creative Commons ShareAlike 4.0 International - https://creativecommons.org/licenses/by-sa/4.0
